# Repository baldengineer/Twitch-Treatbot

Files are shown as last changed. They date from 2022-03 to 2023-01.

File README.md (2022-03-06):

A modified candy dispenser. It connects to Twitch's API using an Adafruit Feather Huzzah. Actions in chat delivers treats to the streamer.

Version 2? was on protoboard but has some power issues.

Version 3 (current) is a carrier for a feather that drives a stepper motor.

## Bald Engineer Live Stream
You can watch this project live (or archived) at https://twitch.tv/baldengineer

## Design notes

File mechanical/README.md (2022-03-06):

3D printed pieces to mount NEMA17 motor at the right height.

You need two of the column supports.

I used 3d heat-set inserts and then connected everything with M2.5 or M3 screws.

## Candy Dispenser
Used a [Zevro Compact Dry Food Dispenser (affiliate link)](https://amzn.to/3MryQym) from Amazon. I removed the knob and put the `Candy Gear` in its place. Then the `Stepper Gear` goes onto the NEMA-17.

## Bald Engineer Live Stream
You can watch this project live (or archived) at https://twitch.tv/baldengineer

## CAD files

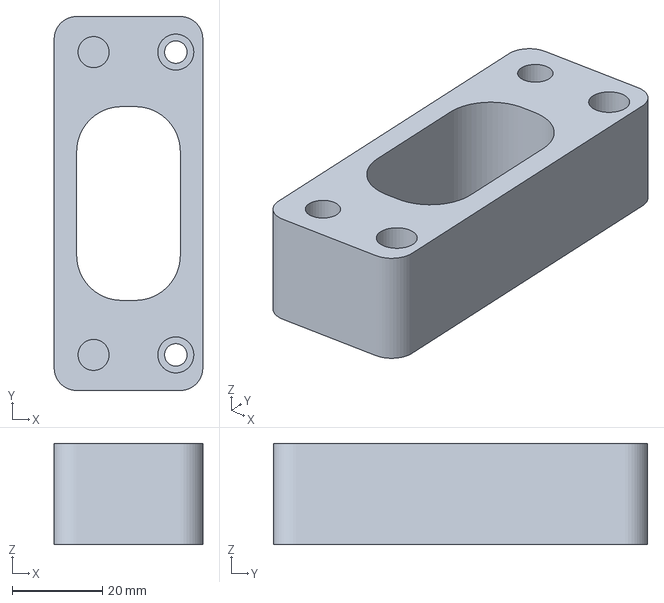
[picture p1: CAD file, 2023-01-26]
mechanical/Smaller Base Plate v6.3mf
33.0 x 83.0 x 22.5 mm

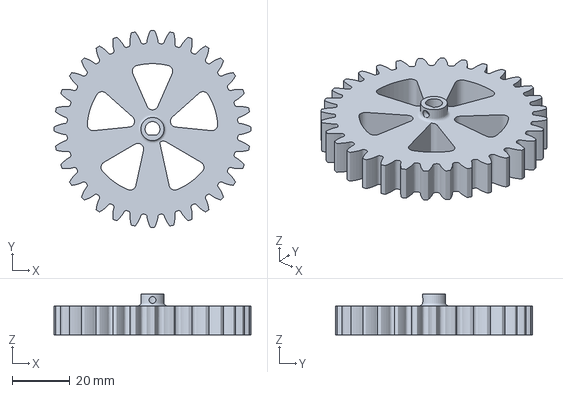
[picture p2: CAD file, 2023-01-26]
mechanical/Stepper Gear v9.3mf
68.0 x 68.0 x 14.0 mm

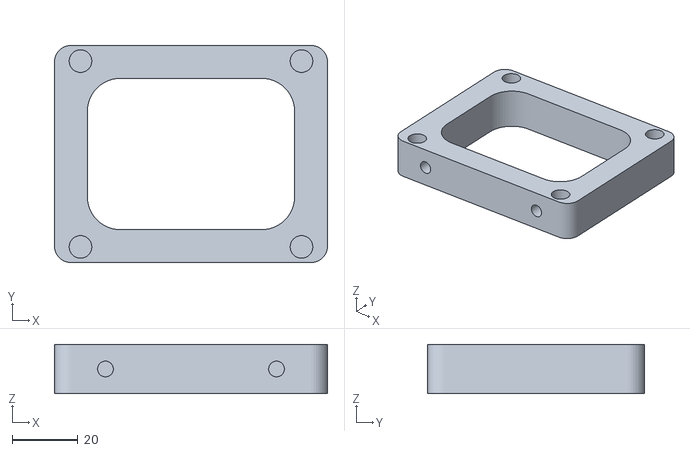
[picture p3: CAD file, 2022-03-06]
mechanical/Base Plate v26.stl
83.0 x 66.0 x 15.0

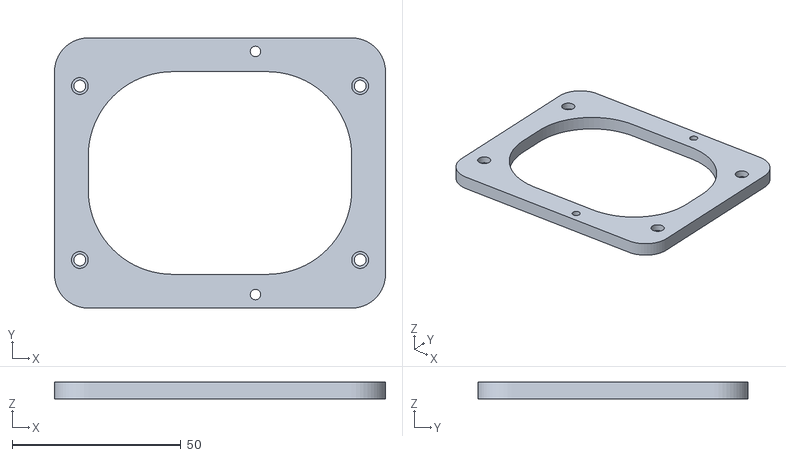
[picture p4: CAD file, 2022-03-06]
mechanical/Column Support rev2 v4.stl
98.0 x 80.0 x 5.00

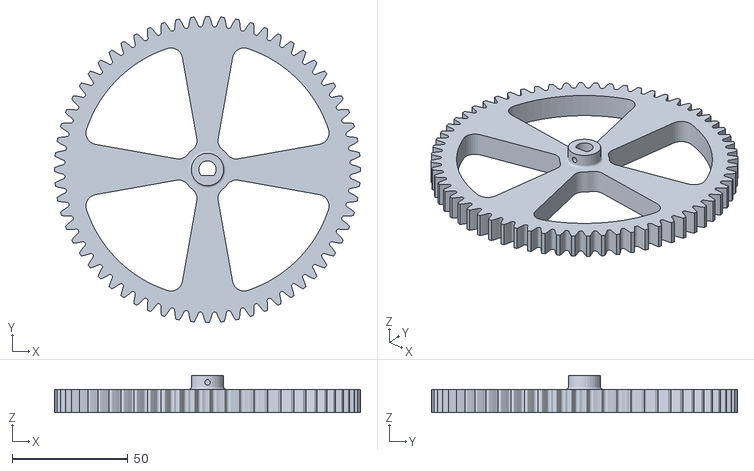
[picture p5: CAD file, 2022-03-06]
mechanical/Candy Gear 128mm v8.stl
132.0 x 132.0 x 16.0

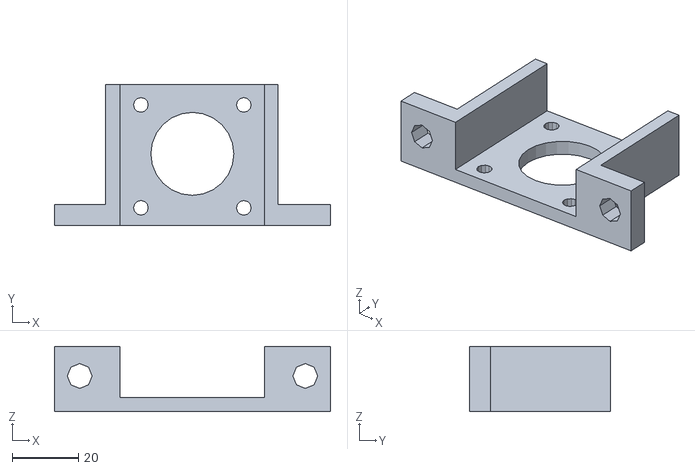
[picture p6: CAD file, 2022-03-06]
mechanical/mtr17 v2.stl
83.2 x 42.4 x 19.7

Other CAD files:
mechanical/Smaller Base Plate v6.stl
mechanical/Stepper Gear v9.stl

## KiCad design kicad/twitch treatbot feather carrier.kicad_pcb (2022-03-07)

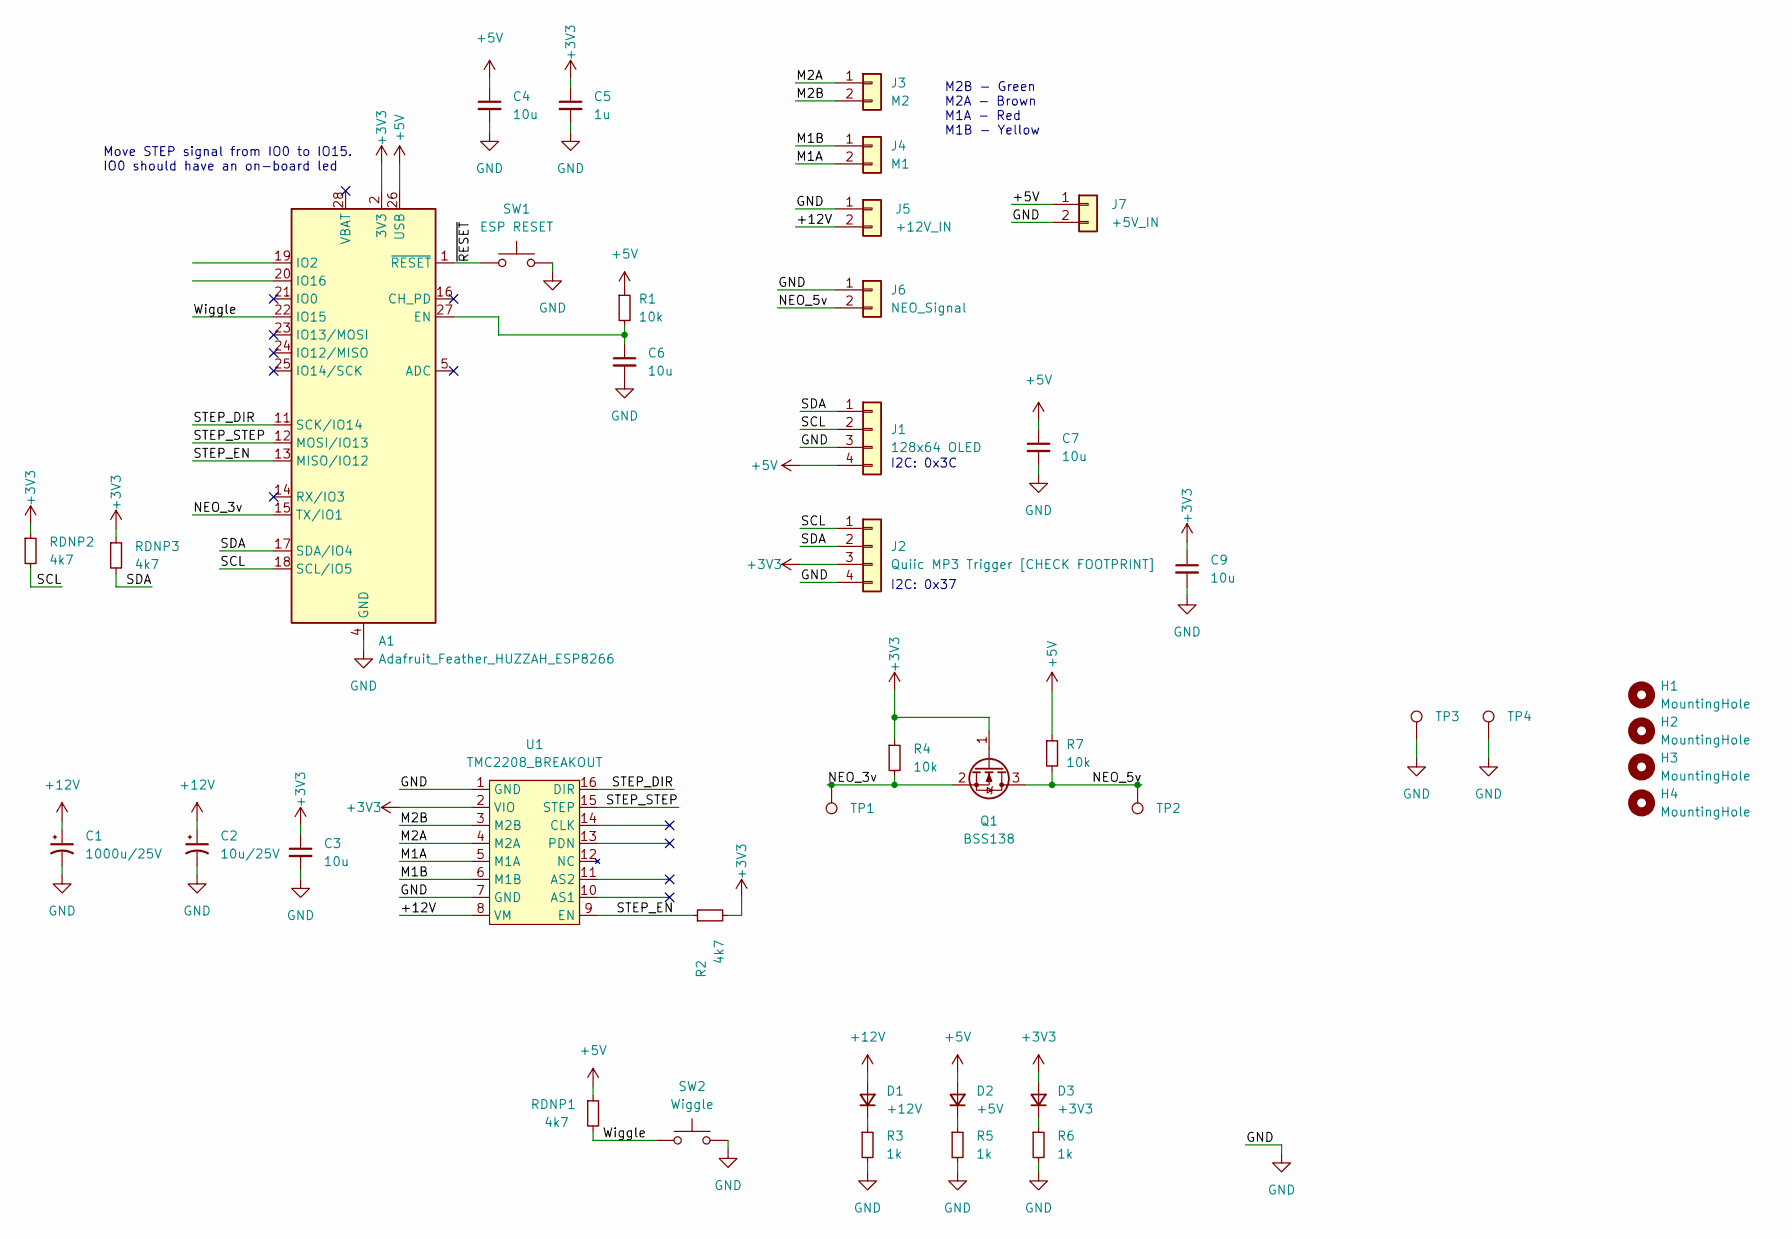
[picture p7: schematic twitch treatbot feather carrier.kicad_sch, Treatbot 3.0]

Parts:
A1: Adafruit_Feather_HUZZAH_ESP8266; Adafruit_Feather
C1: 1000u/25V; CP_Radial_D13.0mm_P5.00mm
C2: 10u/25V; CP_Radial_D8.0mm_P3.80mm
C3, C4, C6, C7, C9: 10u; C_0805_2012Metric
C5: 1u; C_0805_2012Metric
D1: +12V; LED_1206_3216Metric
D2: +5V; LED_1206_3216Metric
D3: +3V3; LED_1206_3216Metric
H1, H2, H3, H4: MountingHole; MountingHole_2.2mm_M2
J1: 128x64 OLED; PinSocket_1x04_P2.54mm_Vertical
J2: Quiic MP3 Trigger [CHECK FOOTPRINT]; PinSocket_1x04_P2.54mm_Vertical
J3: M2; TerminalBlock_Altech_AK300-2_P5.00mm
J4: M1; TerminalBlock_Altech_AK300-2_P5.00mm
J5: +12V_IN; TerminalBlock_Altech_AK300-2_P5.00mm
J6: NEO_Signal; TerminalBlock_Altech_AK300-2_P5.00mm
J7: +5V_IN; PinHeader_1x02_P2.54mm_Vertical
Q1: BSS138; SOT-23
R1, R4, R7: 10k; R_0805_2012Metric
R2: 4k7; R_0805_2012Metric
R3, R5, R6: 1k; R_0805_2012Metric
RDNP1, RDNP2, RDNP3: 4k7; R_0805_2012Metric
SW1: ESP RESET; SW_Push_CK_PTS525_SM15
SW2: Wiggle; SW_Push_CK_PTS525_SM15
TP1, TP2, TP3, TP4: TestPoint_Harwin; Harwin-S1751-46-Test-Point
U1: TMC2208_BREAKOUT; DIP-16_W12.7mm

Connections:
+3V3: A1.2 (3V3), C3.1, C5.1, C9.1, D3.2 (A), J2.3, Q1.1 (G), R2.2, R4.1, RDNP2.1, RDNP3.1, U1.2 (VIO)
+5V: A1.26 (USB), C4.1, C7.1, D2.2 (A), J1.4, J7.1, R1.1, R7.1, RDNP1.1
+12V: C1.1, C2.1, D1.2 (A), J5.2, U1.8 (VM)
/M1A: J4.2, U1.5 (M1A)
/M1B: J4.1, U1.6 (M1B)
/M2A: J3.1, U1.4 (M2A)
/M2B: J3.2, U1.3 (M2B)
/NEO_3v: A1.15 (TX/IO1), Q1.2 (S), R4.2, TP1.1
/NEO_5v: J6.2, Q1.3 (D), R7.2, TP2.1
/SCL: A1.18 (SCL/IO5), J1.2, J2.1, RDNP2.2
/SDA: A1.17 (SDA/IO4), J1.1, J2.2, RDNP3.2
/STEP_DIR: A1.11 (SCK/IO14), U1.16 (DIR)
/STEP_EN: A1.13 (MISO/IO12), R2.1, U1.9 (EN)
/STEP_STEP: A1.12 (MOSI/IO13), U1.15 (STEP)
/Wiggle: A1.22 (IO15), RDNP1.2, SW2.1
/~RESET: A1.1 (~RESET), SW1.1
GND: A1.4 (GND), C1.2, C2.2, C3.2, C4.2, C5.2, C6.2, C7.2, C9.2, J1.3, J2.4, J5.1, J6.1, J7.2, R3.2, R5.2, R6.2, SW1.2, SW2.2, TP3.1, TP4.1, U1.1 (GND), U1.7 (GND)
unnamed: A1.27 (EN), C6.1, R1.2
unnamed: D1.1 (K), R3.1
unnamed: D2.1 (K), R5.1
unnamed: D3.1 (K), R6.1

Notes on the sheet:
Move STEP signal from IO0 to IO15. IO0 should have an on-board led
I2C: 0x37
I2C: 0x3C
M2B - Green M2A - Brown M1A - Red M1B - Yellow

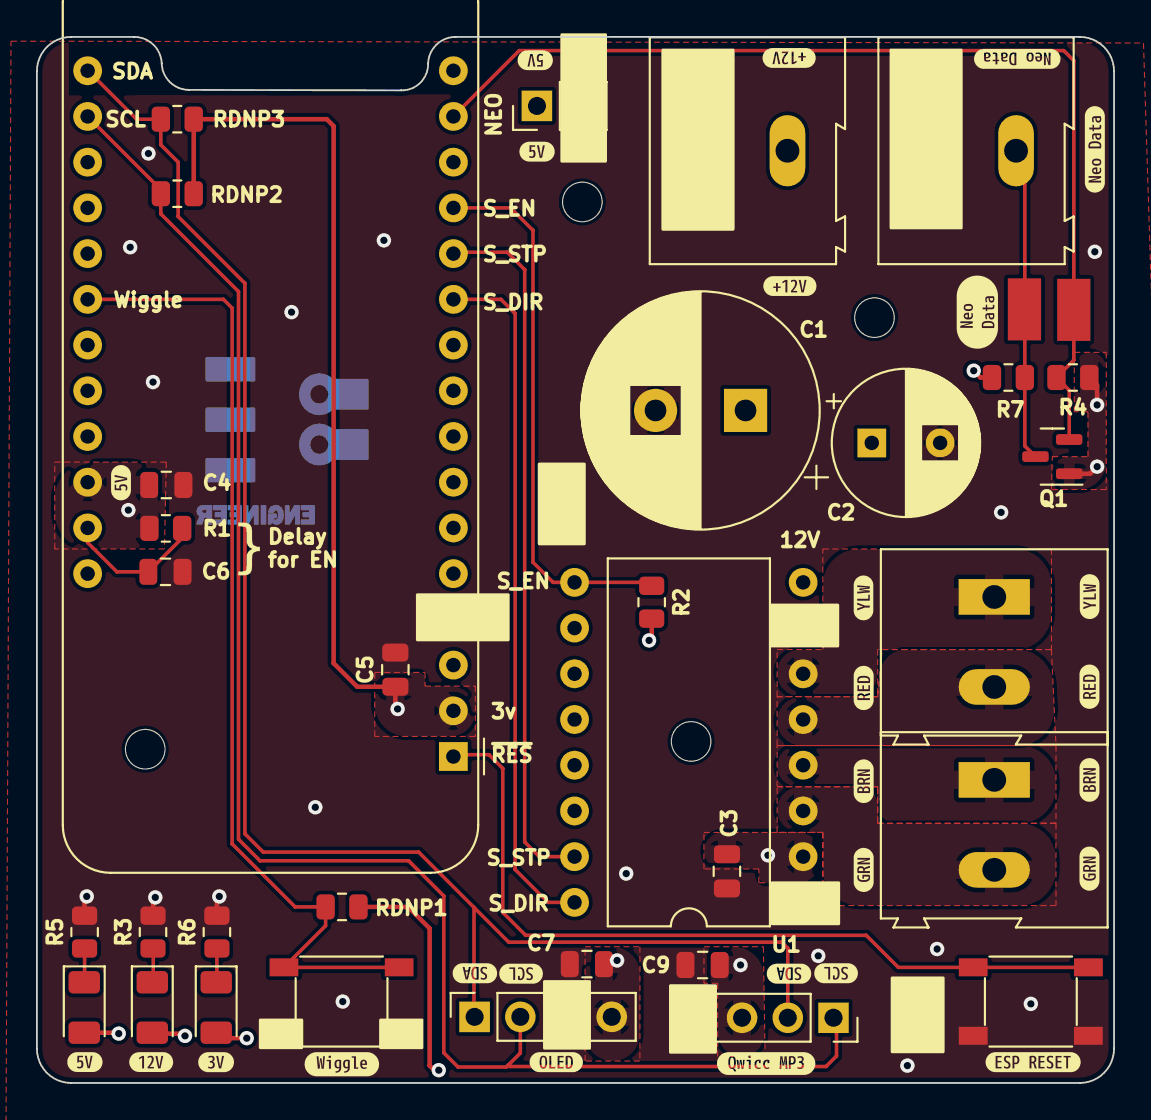
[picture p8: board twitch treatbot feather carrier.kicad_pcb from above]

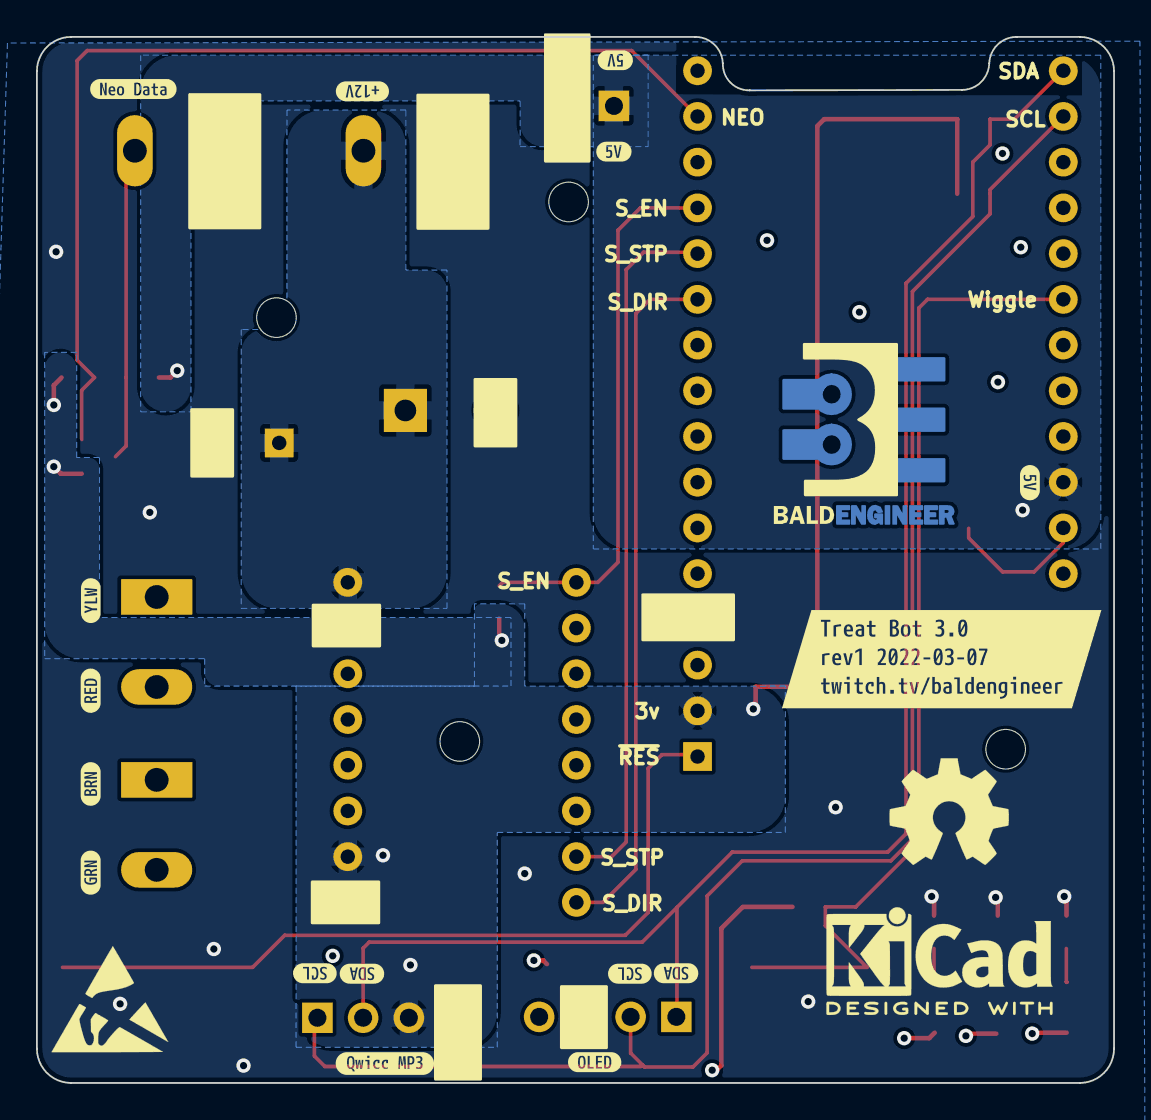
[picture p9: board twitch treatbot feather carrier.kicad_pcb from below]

Board: 4 copper layers, 59.8 x 58.1 mm, 86 parts (17 on the bottom side), 21 nets.

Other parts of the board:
kibuzzard-622632CA: G***; kibuzzard-622632CA
kibuzzard-622632E6: G***; kibuzzard-622632E6
kibuzzard-622632F0, kibuzzard-622632F0#2, kibuzzard-622632F0#3: G***; kibuzzard-622632F0
kibuzzard-622632F9: G***; kibuzzard-622632F9
kibuzzard-622633E5, kibuzzard-622633E5#2, kibuzzard-622633E5#3: G***; kibuzzard-622633E5
kibuzzard-622633FA, kibuzzard-622633FA#2, kibuzzard-622633FA#3: G***; kibuzzard-622633FA
kibuzzard-622634A8, kibuzzard-622634A8#2, kibuzzard-622634A8#3, kibuzzard-622634A8#4: G***; kibuzzard-622634A8
kibuzzard-622642D3: G***; kibuzzard-622642D3
kibuzzard-622647CC: G***; kibuzzard-622647CC
kibuzzard-6226330D, kibuzzard-6226330D#2: G***; kibuzzard-6226330D
kibuzzard-6226331D, kibuzzard-6226331D#2: G***; kibuzzard-6226331D
kibuzzard-62263363: G***; kibuzzard-62263363
kibuzzard-62263378, kibuzzard-62263378#2, kibuzzard-62263378#3, kibuzzard-62263378#4: G***; kibuzzard-62263378
kibuzzard-62263388, kibuzzard-62263388#2, kibuzzard-62263388#3, kibuzzard-62263388#4: G***; kibuzzard-62263388
kibuzzard-62263418, kibuzzard-62263418#2, kibuzzard-62263418#3: G***; kibuzzard-62263418
kibuzzard-62263431, kibuzzard-62263431#2, kibuzzard-62263431#3: G***; kibuzzard-62263431
kibuzzard-62263473: G***; kibuzzard-62263473
kibuzzard-62263481, kibuzzard-62263481#2, kibuzzard-62263481#3: G***; kibuzzard-62263481
kibuzzard-62263491, kibuzzard-62263491#2, kibuzzard-62263491#3: G***; kibuzzard-62263491
svg2mod: G***; BE10v2

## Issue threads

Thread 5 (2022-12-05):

Wiggle button connects to IO15 but cannot be used for push button

baldengineer, 2022-12-05:
IO15 is pulled down on feather.  15 can be used as an output, however.

Had to bodge wiggle to use another IO pin.

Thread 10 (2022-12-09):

Skip MQTT at boot

baldengineer, 2022-12-09:
Skip WiFi and MQTT If Wiggle button is held down during power-on.

And no. This mode is not just so I can get candy when not doing a stream.

Also, this mode is just so I can get candy when not doing a stream.

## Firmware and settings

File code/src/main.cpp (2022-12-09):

#include "main.h"

//extern void handle_treats();
extern void setup_stepper_motor();
extern void setup_pixel_panel();
extern void  process_pixels();

void setup() {
  pinMode(WIGGLE_BTN, INPUT_PULLUP);
  pinMode(KEEPALIVE_LED_Pin, OUTPUT);
  digitalWrite(KEEPALIVE_LED_Pin, HIGH);
  Serial.begin(115200);  // wait for serial, but not for too long.
  Serial.println("Waiting for character");
  while(Serial.available() == 0)
    if (millis() > SERIAL_PORT_WAIT_TIMEOUT)
      break;
  digitalWrite(KEEPALIVE_LED_Pin, LOW);

  setup_oled();
  print_message("TreatBot32");
  setup_stepper_motor();
  setup_pixel_panel();
  setup_mp3();
  setup_wifi();
  setup_mqtt();
}

void loop() {
  mqtt_stay_alive();
  handle_buttons();
  do_motor_tasks();
 // handle_treats();
  do_heartbeat_led();
  process_pixels();
}

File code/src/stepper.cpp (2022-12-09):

#include "treatbot_globals.h"

extern void start_treats_cycle();
extern void mp3_play(int track);
extern void turn_off_scene();
extern bool pixel_panel_enable;
extern uint32_t pixel_previous_millis;

void setup_stepper_motor() {
  print_message("Motor");
  pinMode(STEP_EN_PIN, OUTPUT);
  digitalWrite(STEP_EN_PIN, HIGH);
  pinMode(DIR_PIN, OUTPUT);
  pinMode(STEP_PIN, OUTPUT);
}

void do_heartbeat_led();
extern void candy_test();

bool spin_direction = CW;
bool wiggle_once = false;

void do_motor_tasks() {
  if (wiggle_once) {
    wiggle_once = false;
    print_message("Wiggle");
    start_treats_cycle();
  }
}

void shake_em_mms(int amt, int speed, int shakes) {
  digitalWrite(STEP_EN_PIN, LOW);
  for (int x = 0; x < (shakes - 1); x++) {
    digitalWrite(DIR_PIN, spin_direction);
    for (uint16_t i = amt; i > 0; i--) {
      // processButtons();
      // process_neo();
      do_heartbeat_led();
      digitalWrite(STEP_PIN, HIGH);
      delayMicroseconds(speed);
      digitalWrite(STEP_PIN, LOW);
      delayMicroseconds(speed);
    }
    yield();
    spin_direction = !spin_direction;
  }
  digitalWrite(STEP_EN_PIN, HIGH);
}

void spin_for_treats(bool direction) {
  int amount = SPIN_AMOUNT;
  int speed = SPIN_SPEED;
  digitalWrite(STEP_EN_PIN, LOW);
  digitalWrite(DIR_PIN, direction);

  for (uint16_t i = amount; i > 0; i--) {
    do_heartbeat_led();
    // processButtons();
    // process_neo();
    digitalWrite(STEP_PIN, HIGH);
    delayMicroseconds(speed);
    digitalWrite(STEP_PIN, LOW);
    delayMicroseconds(speed);

  }
  digitalWrite(STEP_EN_PIN, HIGH);
}

void dispense_cycle() {
  //    Almond M&Ms: 350,400,10
  // Hershey Kisses: 600,250,15
  pixel_panel_enable = true;
  pixel_previous_millis = millis();

  mp3_play(3);
  long_delay(2500);
  shake_em_mms(600, 250, 15);
  spin_for_treats(false);
  pixel_panel_enable = false;
  turn_off_scene();
}

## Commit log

2022-03-06 adding v2 enclosure -- probably won't change any for version 3
    [Base Plate v26.stl, Candy Gear 128mm v8.stl, Column Support rev2 v4.stl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]
2022-03-06 blank kicad commit, ignore *.zip because of backups
    [twitch treatbot feather carrier.kicad_pcb, twitch treatbot feather carrier.kicad_sch]
2022-03-07 PCB floorplanning
    [twitch treatbot feather carrier.kicad_pcb, twitch treatbot feather carrier.kicad_sch]
2022-03-07 first floorplan done
    [twitch treatbot feather carrier.kicad_pcb, twitch treatbot feather carrier.kicad_sch]
2022-03-07 2nd floorplan
    [twitch treatbot feather carrier.kicad_pcb, twitch treatbot feather carrier.kicad_sch]
2022-03-07 Layout done, fully routed, most of silk done, debating if to convert to 2 layer board
    [twitch treatbot feather carrier.kicad_pcb, twitch treatbot feather carrier.kicad_sch]
2022-03-07 forgot mounting holes!
    [twitch treatbot feather carrier.kicad_pcb, twitch treatbot feather carrier.kicad_sch]
2022-12-04 added NC to existing pins and made notes after reviewing built design. IO15 was a lousy pick for the Wiggle button.
    [twitch treatbot feather carrier.kicad_sch]
2022-12-04 updated pinouts for new control board. added more status updates to OLED. stepper driver not yet tested.
2022-12-05 removed fast LED because it spams the serial port
2022-12-05 sample config file
2022-12-05 testing multiple definition issue
    [treatbot_globals.h]
2022-12-05 esp32 connects to mqtt with SSL and blinks a LED
2022-12-06 added some stepper stuff
2022-12-06 moar noise maker stuff
    [main.cpp, sound_maker.cpp, treatbot-mqtt.cpp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]
2022-12-09 reworked serial wait to include a character
    [main.cpp, oled.cpp, sound_maker.cpp]
2022-12-09 dispensing on esp32 working
2022-12-09 added noises and got treats
    [main.cpp, sound_maker.cpp, stepper.cpp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]
2023-01-26 updated gears for slightly better fit
    [Smaller Base Plate v6.3mf, Smaller Base Plate v6.stl, Stepper Gear v9.3mf]
